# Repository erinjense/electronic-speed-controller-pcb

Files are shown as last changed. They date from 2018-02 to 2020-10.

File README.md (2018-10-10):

# pwmCat-motorBoard

Multidisciplinary Engineering class with requirements of remote-controlled vehicle design to complete "Cat's Conundrum Obstacle Course".
Spring 2018
Montana State University




EAGLE files for PCB for a motor board based on using the atmega328P microcontroller, DRV8833 motor driver, HM-11 Bluetooth LE module, and LSM6DS3TR accel/gyro.  
The atmega328P is used as a finite state machine for direction and speed control.  
The HM-11 receives a byte encoded with direction and speed from an iPhone user.
The atmega328P outputs Pulse-Width-Modulation(PWM) to the DRV8833, receives HM-11 byte via USART and receives accel/gyro data through I2C.
The board uses 3.3V for every device.  
There is a power kill-switch and jumper pin by the ISP1 to separate incoming 5V from other 3.3V devices when programming atmega328P. (TODO: alternative solution).
TODO: 47 uF capacitor as 0805 too small. Some other capacitors sizing needs tweaking.

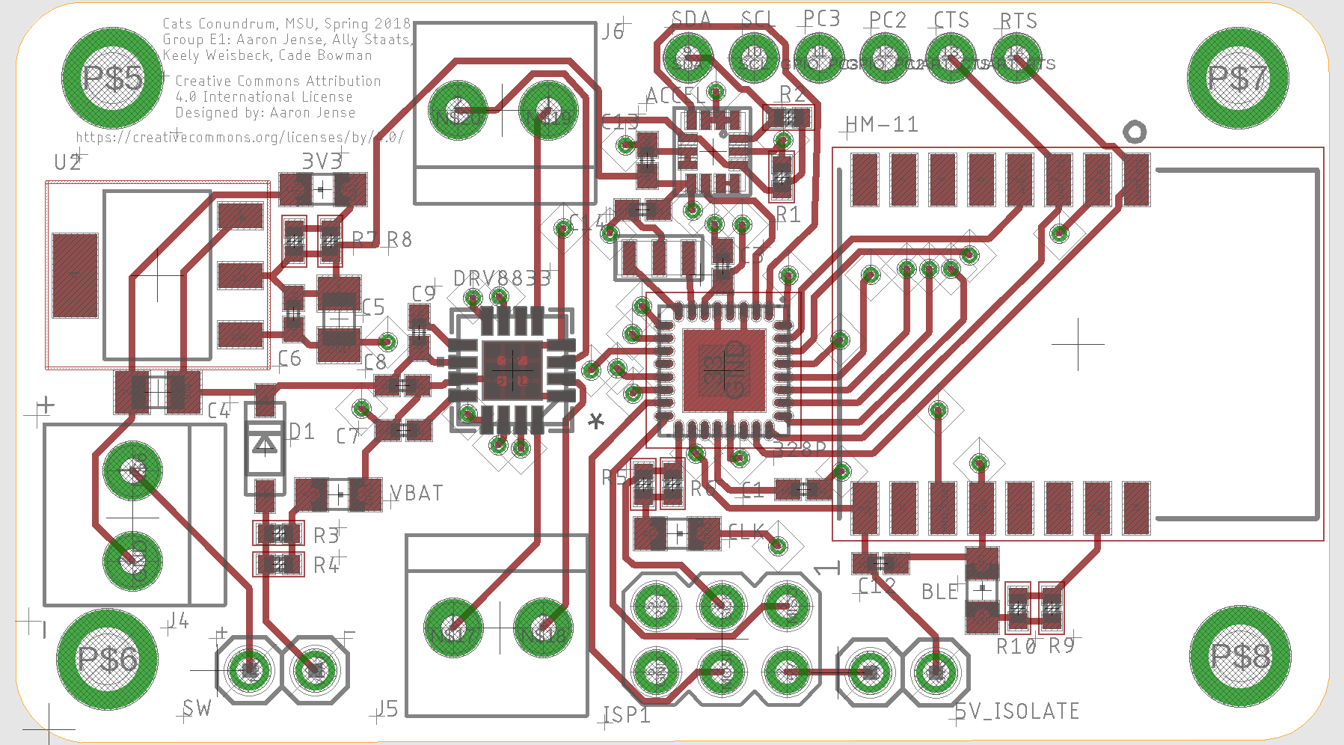
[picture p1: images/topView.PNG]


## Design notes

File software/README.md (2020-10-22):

# Electronic Speed Control Software
A motor driver board was created for a remote-controlled continuous tread vehicle.  

The repository for the EAGLE schematics is "electronic-speed-controller-pcb".

The board contains a DRV8833 motor driver, atmega328p microcontroller and a HM-11 Bluetooth Low Energy module.

This repository is the C-code that was used to control the motors with PWM and USART RX / TX for the HM-11 module.

It is primarily based on a state machine where a direction/speed control signal is received from a bluetooth control device.

The state machine output is Pulse Width Modulation(PWM) to the motor driver for direction/speed.

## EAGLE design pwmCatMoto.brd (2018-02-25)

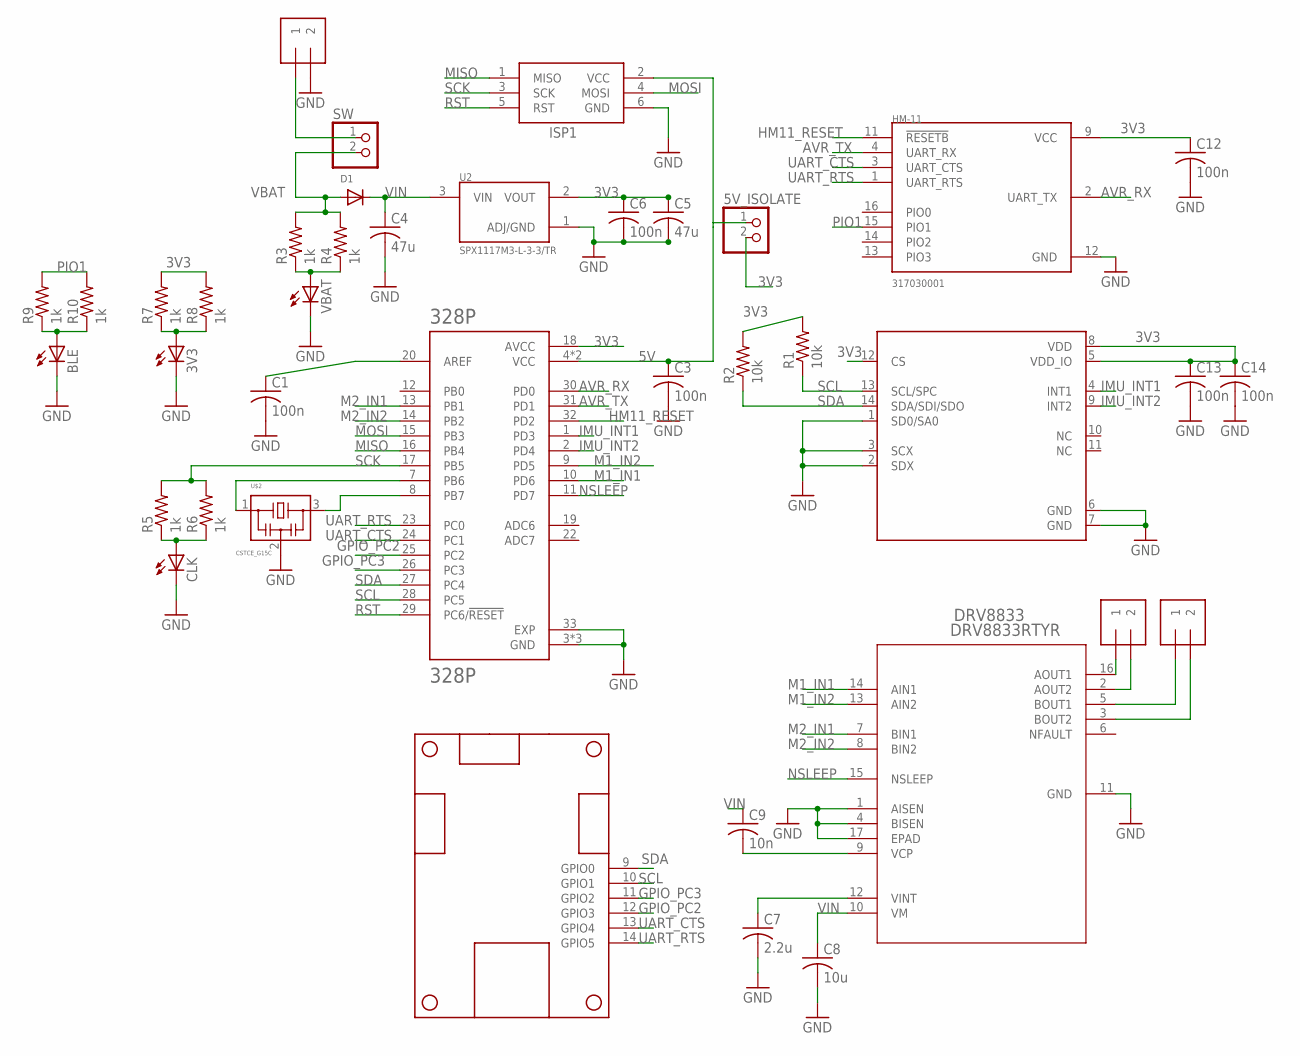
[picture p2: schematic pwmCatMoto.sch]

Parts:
3V3: LEDCHIPLED_0805; CHIPLED_0805
5V_ISOLATE: JUMPER; 1X02
328P: 328P; QFN50P500X500X100-33N
ACCEL: LSM6DS3TR; 14VFLGA_LSM6DS3TR
BLE: LEDCHIPLED_0805; CHIPLED_0805
C1, C3, C6, C12, C13, C14: 100n; C0402K
C4, C5: 47u; C0805K
C7: 2.2u; C0402K
C8: 10u; C0402K
C9: 10n; C0402K
CLK: LEDCHIPLED_0805; CHIPLED_0805
D1: DIODESOD-123; SOD-123
DRV8833: DRV8833RTYR; RTY16
HM-11: 317030001; XCVR_317030001
ISP1: AVRISP-6; AVRISP
J4, J5, J6: 1X2-3.5MM
R1, R2: 10k; R0402
R3, R4, R5, R6, R7, R8, R9, R10: 1k; R0402
SW: KILLSWITCH; 1X02
U2: SPX1117M3-L-3-3/TR; SOT230P700X180-3N
U$1: TANK_BOARD_OUTLINE_GPIO; TANK_BOARD_1
U$2: CSTCE_G15C
VBAT: LEDCHIPLED_0805; CHIPLED_0805

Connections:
3V3: 5V_ISOLATE.2, 328P.18 (AVCC), ACCEL.5 (VDD_IO), ACCEL.8 (VDD), ACCEL.12 (CS), C5.1, C6.1, C12.1, C13.1, C14.1, HM-11.9 (VCC), R1.2, R2.2, R7.2, R8.2, U2.2 (VOUT)
5V: 5V_ISOLATE.1, 328P.4 (VCC), 328P.6 (VCC), C3.1, ISP1.2 (VCC)
AVR_RX: 328P.30 (PD0), HM-11.2 (UART_TX)
AVR_TX: 328P.31 (PD1), HM-11.4 (UART_RX)
GND: 3V3.C, 328P.3 (GND), 328P.5 (GND), 328P.21 (GND), 328P.33 (EXP), ACCEL.1 (SD0/SA0), ACCEL.2 (SDX), ACCEL.3 (SCX), ACCEL.6 (GND), ACCEL.7 (GND), BLE.C, C1.2, C3.2, C4.2, C5.2, C6.2, C7.2, C8.2, C12.2, C13.2, C14.2, CLK.C, DRV8833.1 (AISEN), DRV8833.4 (BISEN), DRV8833.11 (GND), DRV8833.17 (EPAD), HM-11.12 (GND), ISP1.6 (GND), J4.2, U2.1 (ADJ/GND), U$2.2, VBAT.C
GPIO_PC2: 328P.25 (PC2), U$1.12 (GPIO3)
GPIO_PC3: 328P.26 (PC3), U$1.11 (GPIO2)
HM11_RESET: 328P.32 (PD2), HM-11.11 (!RESETB)
IMU_INT1: 328P.1 (PD3), ACCEL.4 (INT1)
IMU_INT2: 328P.2 (PD4), ACCEL.9 (INT2)
M1_IN1: 328P.10 (PD6), DRV8833.14 (AIN1)
M1_IN2: 328P.9 (PD5), DRV8833.13 (AIN2)
M2_IN1: 328P.13 (PB1), DRV8833.7 (BIN1)
M2_IN2: 328P.14 (PB2), DRV8833.8 (BIN2)
MISO: 328P.16 (PB4), ISP1.1 (MISO)
MOSI: 328P.15 (PB3), ISP1.4 (MOSI)
unnamed: C7.1, DRV8833.12 (VINT)
unnamed: 328P.7 (PB6), U$2.1
unnamed: 328P.8 (PB7), U$2.3
unnamed: 328P.20 (AREF), C1.1
unnamed: C9.2, DRV8833.9 (VCP)
unnamed: J4.1, SW.1
unnamed: R3.1, R4.1, VBAT.A
unnamed: BLE.A, R9.1, R10.1
unnamed: CLK.A, R5.1, R6.1
unnamed: 3V3.A, R7.1, R8.1
unnamed: DRV8833.16 (AOUT1), J5.1
unnamed: DRV8833.2 (AOUT2), J5.2
unnamed: DRV8833.5 (BOUT1), J6.1
unnamed: DRV8833.3 (BOUT2), J6.2
NC: ACCEL.10 (NC), ACCEL.11 (NC)
NSLEEP: 328P.11 (PD7), DRV8833.15 (NSLEEP)
PIO1: HM-11.15 (PIO1), R9.2, R10.2
RST: 328P.29 (PC6/!RESET), ISP1.5 (RST)
SCK: 328P.17 (PB5), ISP1.3 (SCK), R5.2, R6.2
SCL: 328P.28 (PC5), ACCEL.13 (SCL/SPC), R1.1, U$1.10 (GPIO1)
SDA: 328P.27 (PC4), ACCEL.14 (SDA/SDI/SDO), R2.1, U$1.9 (GPIO0)
UART_CTS: 328P.24 (PC1), HM-11.3 (UART_CTS), U$1.13 (GPIO4)
UART_RTS: 328P.23 (PC0), HM-11.1 (UART_RTS), U$1.14 (GPIO5)
VBAT: D1.A, R3.2, R4.2, SW.2
VIN: C4.1, C8.1, C9.1, D1.C, DRV8833.10 (VM), U2.3 (VIN)

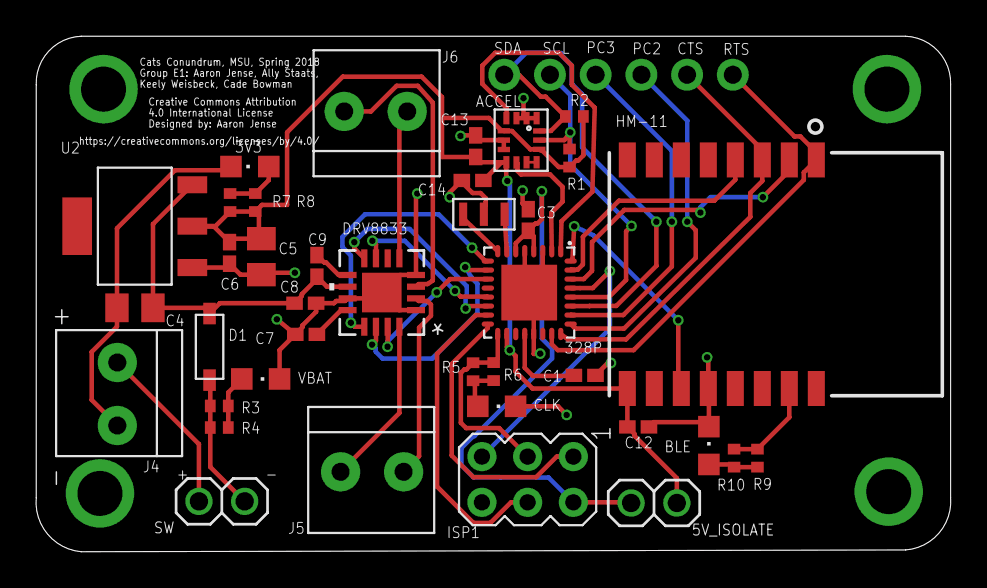
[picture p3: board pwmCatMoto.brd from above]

Board: 2 copper layers, 50.8 x 28.6 mm, 39 parts (0 on the bottom side), 41 nets.

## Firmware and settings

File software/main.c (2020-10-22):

/* Direction and Speed Finite State Machine
 *
 * Designed for pwmCat-motorBoard
 *
 * Receives a Bluetooth Low Energy (BLE) signal
 * from an iPhone app or any other BLE capable device
 * connected and transmiting the correct ASCII letter/number.
 *
 * Code was designed for discrete signals. e.g. ( The user
 * presses a forward arrow on an app. The app sends 'F' to 
 * the BLE module on motor board. The atmega328p receives
 * signal from the BLE module via UART.
 * This code then drives motors to go in a forward direction.
 * The code will remain in forward direction unless the user
 * changes direction.)
 *
 * DIRECTION SIGNALS:
 *
 * forward: 'F'
 * backward: 'B'
 * right: 'R'
 * left: 'L'
 *
 * SPEED SIGNALS:
 *
 * stop : '0'
 * slow : '1'
 * mid : '2'
 * max : '3'
 *
 */


#include <avr/io.h>
#include <avr/interrupt.h>
#include "pinDefines.h"
#include <util/delay.h>
#include "USART.h"
#include "PWM.h"

#define UBRR_VALUE (((F_CPU / (USART_BAUDRATE * 16UL))) - 1)
#define USART_BAUDRATE 9600

/* Delays so that the motors don't instantly go from max speed
 * to stop or change direction instatnly at high speeds.
 * This helps prevent current spikes
 */
#define MOTOR_SYNC_DELAY 5
#define SPEED_STEP_DELAY 2

#define MAX_SPEED 50
#define MED_SPEED 100
#define SLOW_SPEED 191
#define STOP_SPEED 255
#define SAFE_SPEED 150

/* Changes speed in steps with safety delays */
void change_speed(uint8_t new_speed) {

  while (OCR0A != new_speed) {
    if (OCR0A < new_speed) { 
      OCR0A++; 
      OCR0B = OCR0A; 
      OCR1A = OCR0A;
      OCR1B = OCR0A;
      _delay_ms(SPEED_STEP_DELAY);
    }
    else if (OCR0A > new_speed) { 
      OCR0A--; 
      OCR0B = OCR0A; 
      OCR1A = OCR0A;
      OCR1B = OCR0A;
      _delay_ms(SPEED_STEP_DELAY);
    }
  }

}
int main(void) {
  uint8_t rx_byte;
  uint8_t current_speed;
  uint8_t last_speed;
  /* Data Direction inits for PortB and PortD */
  DDRB |= ((1 << PB1) | (1 << PB2) | (1 << PB5));
  DDRD |= ((1 << PD2) | (1 << PD5) | (1 << PD6) | (1 << PD7));
  /* nSleep ON for DRV8833 = motor output ON */
  PORTD |= (1 << PD7);

  initPWM();
  initUSART();

  current_speed = 150;
  last_speed = current_speed;

  OCR0A = current_speed;
  OCR0B = OCR0A;
  OCR1A = OCR0A;
  OCR1B = OCR0A;

  printString("AT+NAMEpwmCat");

  while(1) {

    /* No user-signal, STOP the motors
     * This would be handy if user control app
     * continuously sends a signal if user
     * continuously holds down a button, but
     * the motors need to stop if user is not
     * sending a signal.
     */
   /* 
    if ( (UCSR0A & 0b10000000) == 0b00000000) {
      change_speed(STOP_SPEED);  
    }
    */

    // Wait forever until user-signal and get it
    rx_byte = receiveByte();

    switch (rx_byte) {

      // Forward
      case 'F':

        /* Always enable motor driver. In case user is
         * going from stop and then changed direction */
        PORTD |= (1 << PD7);

        if (current_speed == STOP_SPEED) {
          forwardPWM();
          current_speed = last_speed;
          change_speed(current_speed);
        }
        /* max speed is 0 and min speed is 255
         * This checks to see if current speed 
         * is higher than a safe speed.
         * The comparison operators are non-intuitive
         */
        else if (current_speed < SAFE_SPEED) {
          change_speed(SAFE_SPEED);
          forwardPWM();
          change_speed(current_speed);
        }
        else { forwardPWM(); }
        break;

      // Backward
      case 'B':
        PORTD |= (1 << PD7);
        if (current_speed == STOP_SPEED) {
          reversePWM();
          current_speed = last_speed;
          change_speed(current_speed);
        }
        else if (current_speed < SAFE_SPEED) {
          change_speed(SAFE_SPEED);
          reversePWM();
          change_speed(current_speed);
        }
        else { reversePWM(); }
        break;

      // Right
      case 'R':
        PORTD |= (1 << PD7);
        if (current_speed == STOP_SPEED) {
          rightPWM();
          current_speed = last_speed;
          change_speed(current_speed);
        }
        else if (current_speed < SAFE_SPEED) {
          change_speed(SAFE_SPEED);
          rightPWM();
          change_speed(current_speed);
        }
        else { rightPWM(); }
        break;
      // Left
      case 'L':
        PORTD |= (1 << PD7);
        if (current_speed == STOP_SPEED) {
          leftPWM();
          current_speed = last_speed;
          change_speed(current_speed);
        }
        else if (current_speed < SAFE_SPEED) {
          change_speed(SAFE_SPEED);
          leftPWM();
          change_speed(current_speed);
        }
        else { leftPWM(); }
        break;
    }

    // Change Speed State
    switch(rx_byte) {

      // Stop
      case '0':
        /* Disable motor driver output */
        PORTD &= ~(1 << PD7);
        /* keep track of last speed, so that
         * if user pressed stop and then changes
         * direction. Then last speed remains same.*/
        last_speed = current_speed;
        current_speed = STOP_SPEED;
        change_speed(current_speed); 
        break;
      // Slowest
      case '1':
        current_speed = SLOW_SPEED;
        change_speed(current_speed);
        break;
      // Medium
      case '2':
        current_speed = MED_SPEED;
        change_speed(current_speed); 
        break;
      // Fastest
      case '3':
        current_speed = MAX_SPEED;
        change_speed(current_speed); 
        break;
    }

  }
  /* Code never reaches here */
  return(0);
}

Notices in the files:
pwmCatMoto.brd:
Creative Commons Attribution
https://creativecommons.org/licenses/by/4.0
